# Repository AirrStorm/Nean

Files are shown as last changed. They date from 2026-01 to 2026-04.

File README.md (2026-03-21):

# Nean
A custom made 3d printed tendon driven robotic hand made to learn more about mechanical designs and a bit of biology. It is loosely based on how the human hand actually works. It uses strings to pull the fingers open and close similar to real muscles in the palm. It uses a python script to read finger positions and controls the movement of the hand.

---

## 🧰 Parts Needed

- Arduino Uno
- 2 18650 li-ion batteries
- Switch
- 16-Channel 12-bit PWM/Servo Driver - PCA9685
- 5 MG90s servos
- Elastic Cord
- Fishing Line
- Buck Converter LM2596S
  
---

## Wiring
Here is a preview of the wiring:

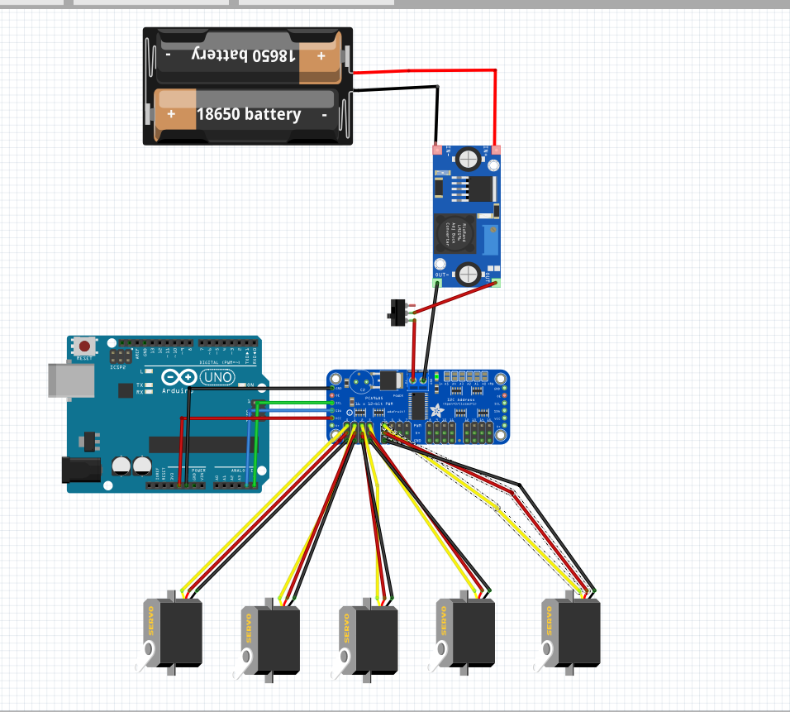
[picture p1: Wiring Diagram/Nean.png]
Wiring Preview


You can find the wiring diagram here:
```
Nean/
├── Wiring Diagram/
   └── Nean.png
```

---

## 3d Models
You can find the STEP files here:

```
Nean/
└──  STEP files/
```
And the STL files here:

```
Nean/
└──  STL files/
```
When 3d printing the models, for the fingers, only 3d print the parts that have "phalanx" at the end, the ones with "Finger" at the end are the full models of the fingers if you want to make changes. And for the arm models, print everything except the "Arm.step" file, which is the full 3d model of the arm if you want to make changes.

Here is a preview of the 3d model:



--- 

## Firmware

You can find the firmware files at:
```
Nean/
└──  Code/
```
It consist of a python file that runs on yout computer and one you upload to the Arduino.
The control system is simple, the python file checks if you hand is open or closed an sends it to the Arduino via serial communication (I plan to change to wifi later)

---

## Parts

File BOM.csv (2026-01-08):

Electronics
Item No. | Quantitiy | Part Name | Source | Links | Price
1 | 1 | ESP 32 | AliExpress | https://www.aliexpress.com/item/1005006984793820.html | $4.56
2 | 1 | PCA9685 Servo Driver | AliExpress | https://www.aliexpress.com/item/1005009595510490.html | $5.71
3 | 1 | DC-DC Buck Converter | AliExpress | https://www.aliexpress.com/item/1005007514313234.html | $3
4 | 1 | TP4056 Charger Module | AliExpress | https://www.aliexpress.com/item/1005009438302489.html | $4
5 | 1 | Slide Switch | Nauvitel Electronics (Local Vendor) | https://nauvitel.com/product/mini-slide-switch/ | $0.50
6 | 2 | 18650 Li-ion Battery | Oku Electronics (Local Vendor) | https://www.okuelectronics.com/store/prototyping/18650-2000mah-round-end-rechargeable-lithium-battery-3-7v-2pcs/ | $10
Actuation
Item No. | Quantity | Part Name | Source | Links | Price
7 | 5 | MG996R Servo | Alixpress | https://www.aliexpress.com/item/1005008658530145.html | $25.31
8 | 1 | Elastic Cord (10 meters) | Alixpress | https://www.aliexpress.com/item/1005008804282381.html | $5.19
9 | 1 | Fishing Line (1.0-0.165mm-5.39LB) | Alixpress | https://www.aliexpress.com/item/1005005245756703.html | $2.74
Wiring
Item No. | Quantity | Part Name | Source | Links | Price
10 | 1 | 2 x 18650 Battery Holder | Nauvitel Electronics (Local Vendor) | https://nauvitel.com/product/18650-3-7v-battery-holder-single/ | $1.50
11 | 5 | Servo Extension Cables (300mm) | AliExpress | https://www.aliexpress.com/item/32921410942.html | $2.26
12 | - | Jumper Wires
Tools and Miscellaneous
Item No. | Quantity | Part Name | Source | Links | Price
13 | 50 | 5 x 2 neodymium magnets | AliExpress | https://www.aliexpress.com/item/1005009966591112.html | $5.72
14 | 1 | Soldering Iron
15 | 1 | Hot glue gun
 | TOTAL | $70.68

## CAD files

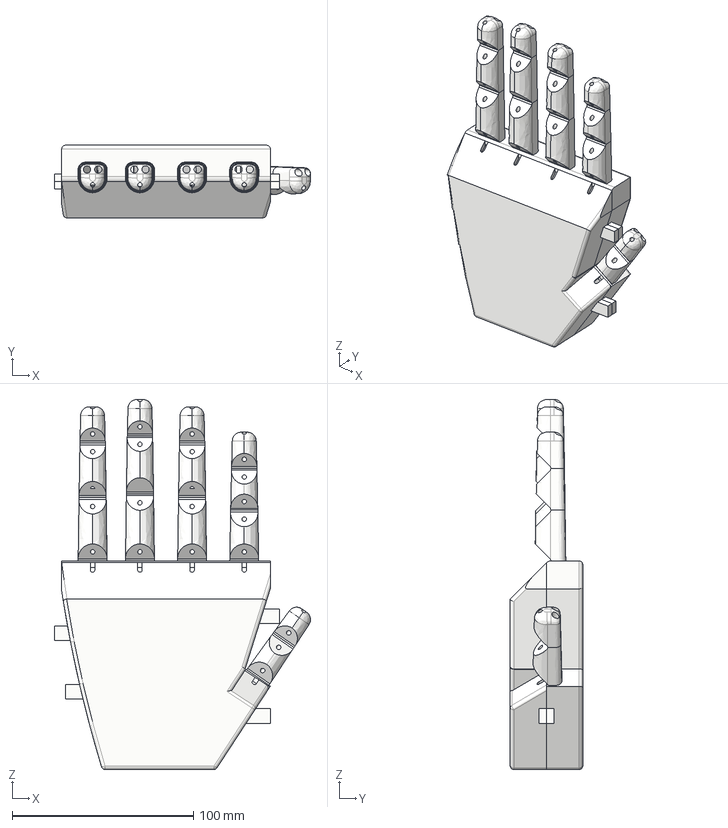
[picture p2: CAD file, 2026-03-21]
STEP files/Hand.step
141.2 x 40.0 x 204.0 mm
Index distal
Index middle
Index proximal
Middle distal
Middle middle
Middle proximal
Ring distal
Ring Middle
Ring proximal
Pinky middle
Pinky proximal
Pinky distal
Thumb distal
Thumb proximal

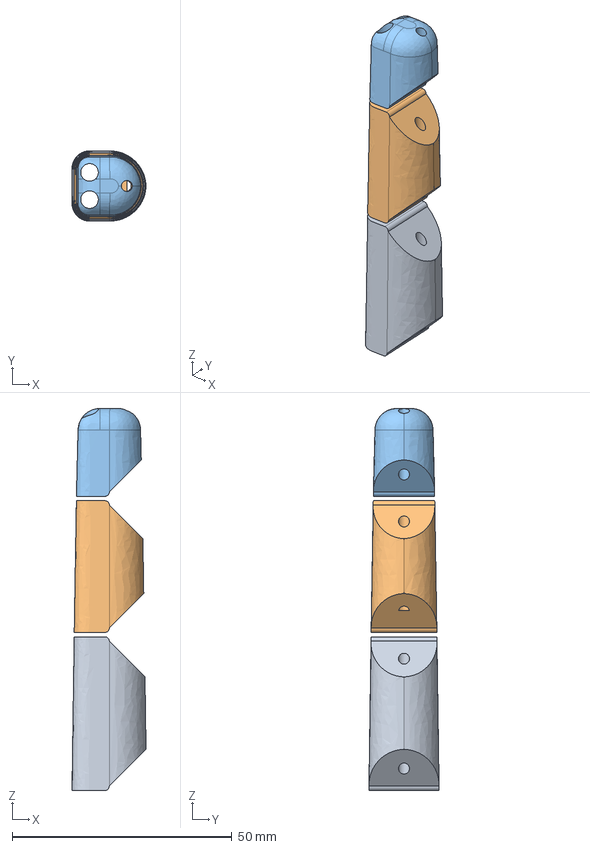
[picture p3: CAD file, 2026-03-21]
STEP files/Parts/Index Finger.step
16.9 x 16.0 x 87.0 mm
Proximal phalanx
Middle phalanx
Distal phalanx

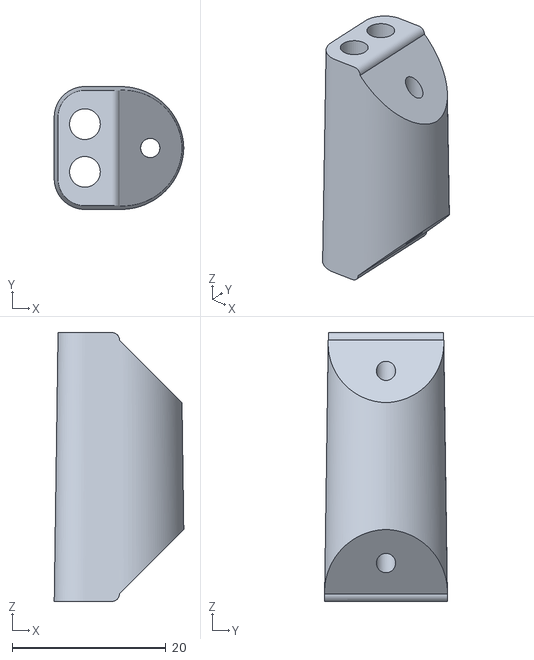
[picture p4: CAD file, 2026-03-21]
STL files/Index proximal phalanx.stl
16.9 x 16.0 x 35.0

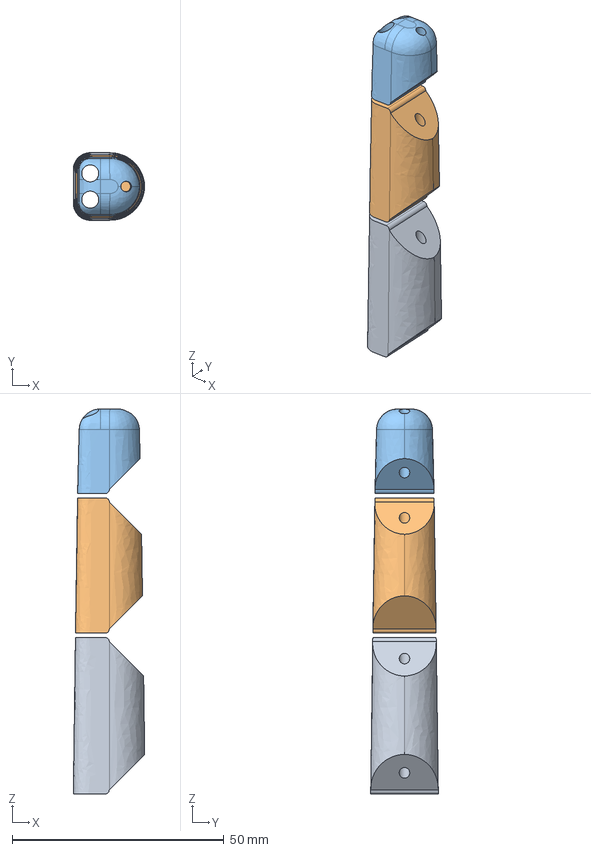
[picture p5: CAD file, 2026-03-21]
STEP files/Parts/Middle Finger.step
16.9 x 16.0 x 91.0 mm
Proximal phalanx
Middle phalanx
Distal phalanx

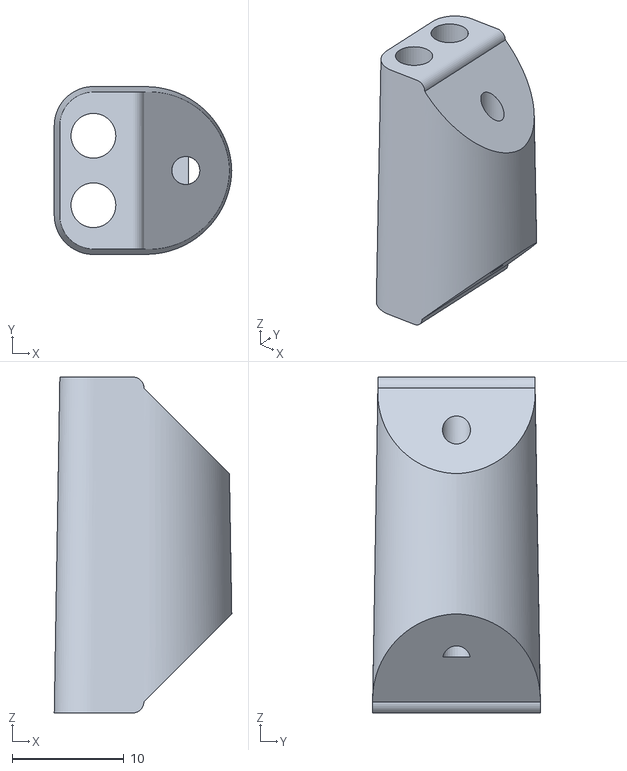
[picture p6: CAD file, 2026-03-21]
STL files/Index middle phalanx.stl
15.9 x 15.0 x 30.0

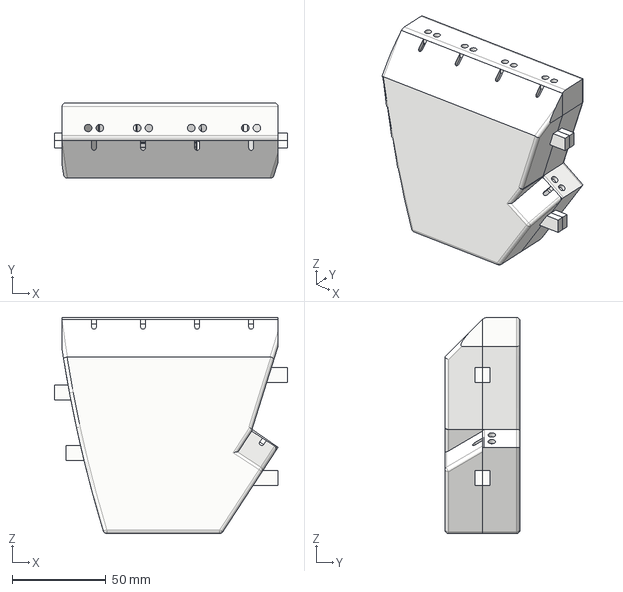
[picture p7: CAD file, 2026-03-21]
STEP files/Parts/Palm.step
124.0 x 40.0 x 115.0 mm

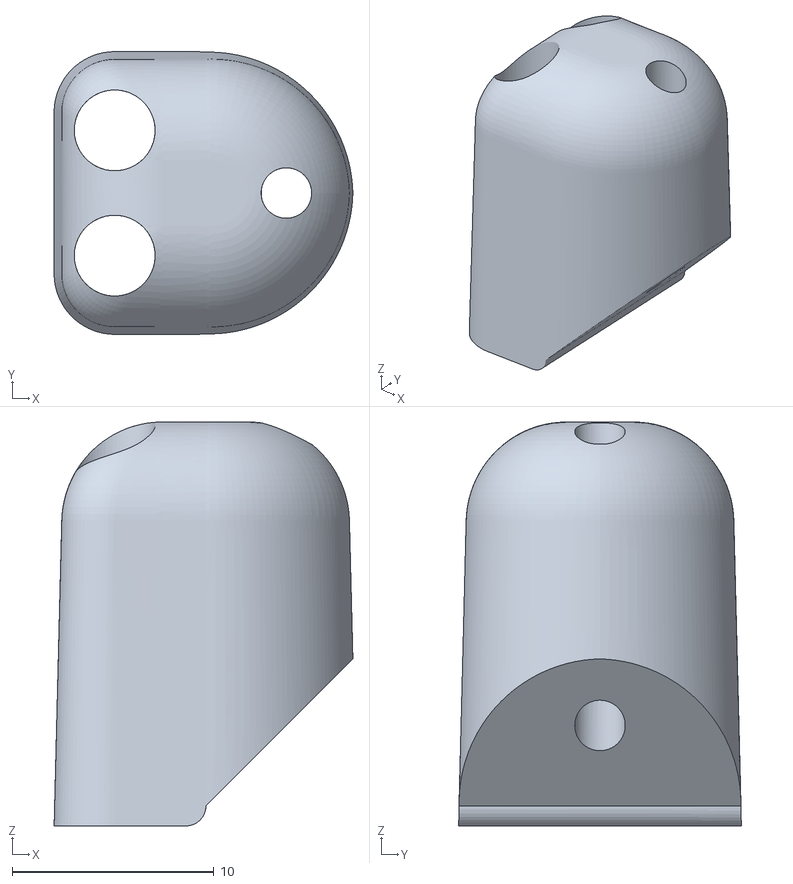
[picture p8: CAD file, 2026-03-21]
STL files/Index distal phalanx.stl
14.8 x 14.0 x 20.0

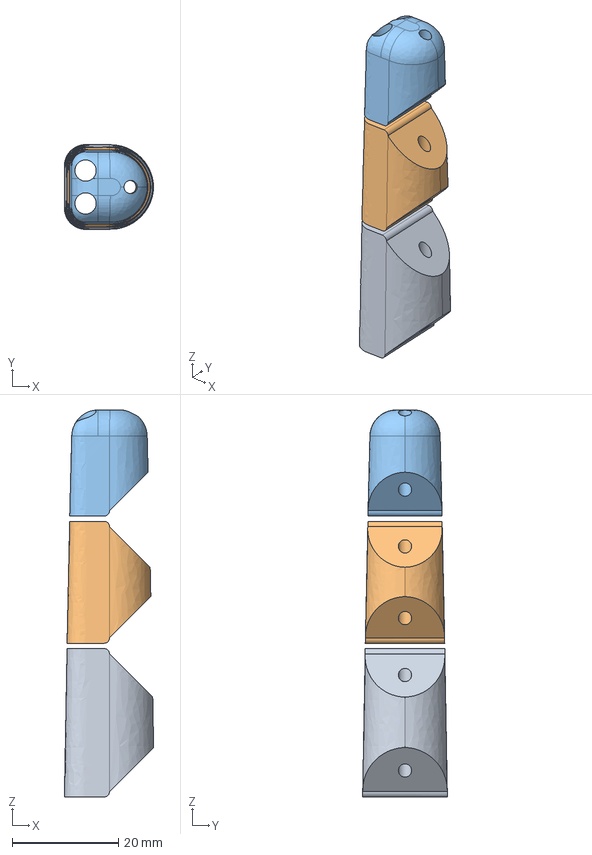
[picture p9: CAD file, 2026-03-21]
STEP files/Parts/Pinky Finger.step
16.8 x 16.0 x 73.0 mm
Proximal phalanx
Middle phalanx
Distal phalanx

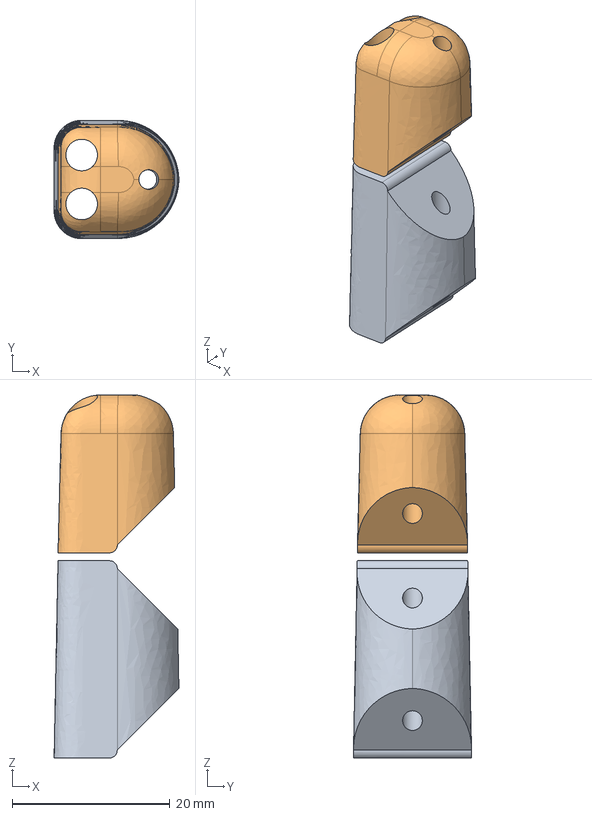
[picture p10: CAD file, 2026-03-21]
STEP files/Parts/Thumb.step
15.8 x 15.0 x 46.0 mm
Middle phalanx
Distal phalanx

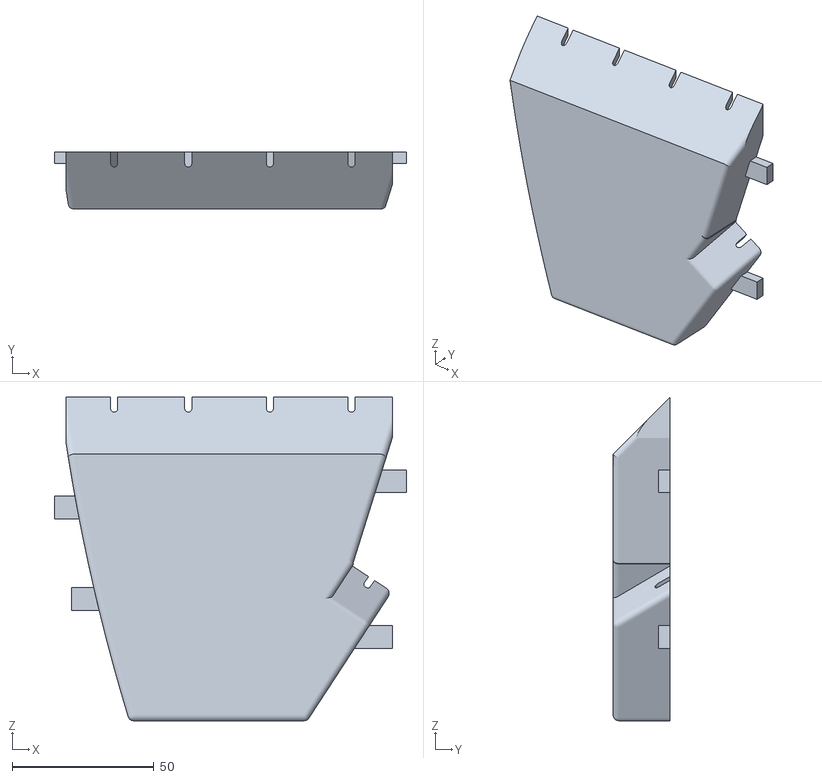
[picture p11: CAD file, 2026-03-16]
STL files/Palm 2.stl
124.0 x 20.0 x 114.0

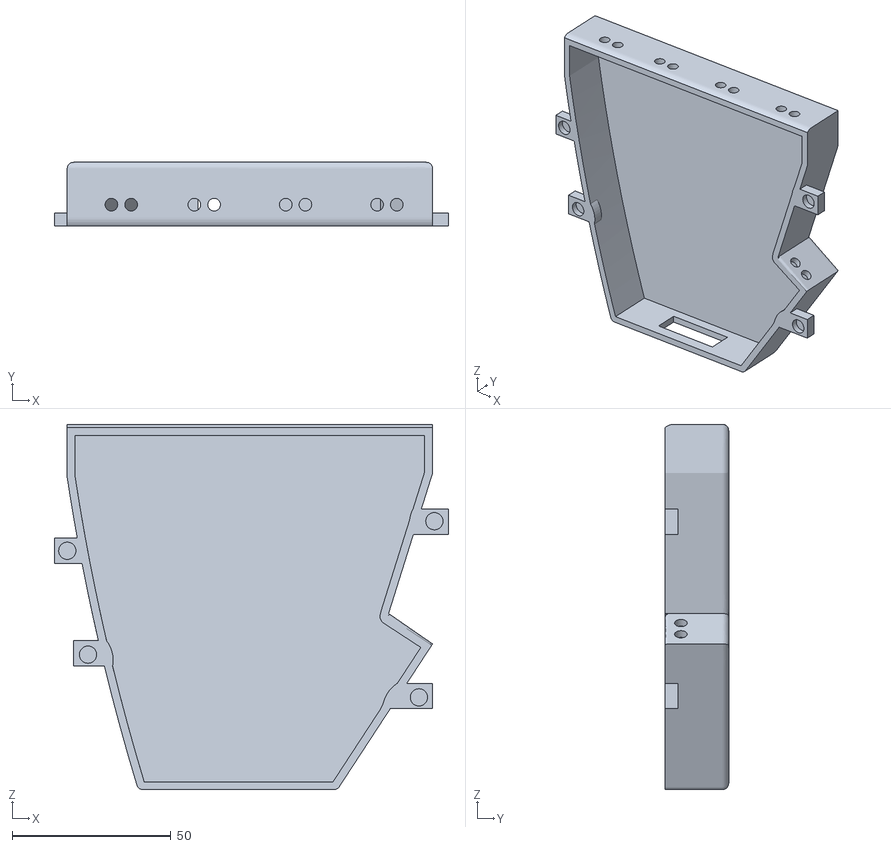
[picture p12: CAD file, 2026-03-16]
STL files/Palm 1.stl
124.0 x 20.0 x 115.0

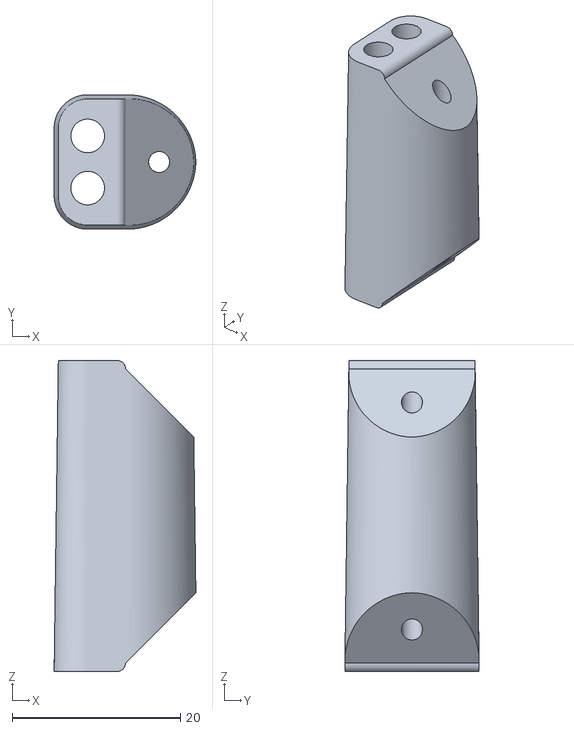
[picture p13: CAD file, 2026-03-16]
STL files/Middle proximal phalanx.stl
16.9 x 16.0 x 37.0

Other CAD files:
STL files/Ring middle phalanx.stl
STEP files/Parts/Ring Finger.step
STL files/Ring distal phalanx.stl
STL files/Pinky distal phalanx.stl
STL files/Thumb distal phalanx.stl
STL files/Ring proximal phalanx.stl
STL files/Middle distal phalanx.stl
STL files/Middle middle phalanx.stl
STL files/Pinky middle phalanx.stl
STL files/Pinky proximal phalanx.stl
STL files/Thumb proximal phalanx.stl

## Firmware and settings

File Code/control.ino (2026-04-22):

#include <Wire.h>
#include <Adafruit_PWMServoDriver.h>

Adafruit_PWMServoDriver pwm = Adafruit_PWMServoDriver();

#define SERVOMIN 110
#define SERVOMAX 640
#define SERVO_FREQ 50

// Channels
#define THUMB  0
#define INDEX  1
#define MIDDLE 2
#define RING   3
#define PINKY  4

uint16_t angleToPulse(int angle) {
  return map(angle, 0, 180, SERVOMIN, SERVOMAX);
}

void setup() {
  Serial.begin(115200);
  pwm.begin();
  pwm.setPWMFreq(SERVO_FREQ);
  delay(10);

  // Start all fingers open
  pwm.setPWM(THUMB,  0, angleToPulse(0));
  pwm.setPWM(INDEX,  0, angleToPulse(0));
  pwm.setPWM(MIDDLE, 0, angleToPulse(0));
  pwm.setPWM(RING,   0, angleToPulse(130));
  pwm.setPWM(PINKY,  0, angleToPulse(130));
}

void loop() {
  if (Serial.available()) {

    String data = Serial.readStringUntil('\n');

    // -------------------
    // THUMB
    // -------------------
    if (data.indexOf("thumb:closed") >= 0) {
      pwm.setPWM(THUMB, 0, angleToPulse(130));
    }
    if (data.indexOf("thumb:open") >= 0) {
      pwm.setPWM(THUMB, 0, angleToPulse(0));
    }

    // -------------------
    // INDEX (uses swapped logic)
    // -------------------
    if (data.indexOf("index:closed") >= 0) {
      pwm.setPWM(INDEX, 0, angleToPulse(130));
    }
    if (data.indexOf("index:open") >= 0) {
      pwm.setPWM(INDEX, 0, angleToPulse(0));
    }

    // -------------------
    // MIDDLE (same as index)
    // -------------------
    if (data.indexOf("middle:closed") >= 0) {
      pwm.setPWM(MIDDLE, 0, angleToPulse(130));
    }
    if (data.indexOf("middle:open") >= 0) {
      pwm.setPWM(MIDDLE, 0, angleToPulse(0));
    }

    // -------------------
    // RING (opposite logic)
    // -------------------
    if (data.indexOf("ring:closed") >= 0) {
      pwm.setPWM(RING, 0, angleToPulse(0));
    }
    if (data.indexOf("ring:open") >= 0) {
      pwm.setPWM(RING, 0, angleToPulse(130));
    }

    // -------------------
    // PINKY (same as ring)
    // -------------------
    if (data.indexOf("pinky:closed") >= 0) {
      pwm.setPWM(PINKY, 0, angleToPulse(0));
    }
    if (data.indexOf("pinky:open") >= 0) {
      pwm.setPWM(PINKY, 0, angleToPulse(130));
    }
  }
}

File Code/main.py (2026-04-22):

import serial
import time

#Uncomment if on Wayland
# import os
# os.environ["QT_QPA_PLATFORM"] = "xcb"


## Import stuff
import cv2 as cv
import mediapipe as mp
from mediapipe.tasks import python
from mediapipe.tasks.python import vision
from math import sqrt


ser = serial.Serial('/dev/ttyACM0', 115200)

cam = cv.VideoCapture(0)
BaseOptions = mp.tasks.BaseOptions
HandLandmarker = mp.tasks.vision.HandLandmarker
HandLandmarkerOptions = mp.tasks.vision.HandLandmarkerOptions
HandResult = mp.tasks.vision.HandLandmarkerResult
VisionRunningMode = mp.tasks.vision.RunningMode


latest_result = None
latest_hand = None
latest_frame = None


def print_result(result: HandResult, output_image: mp.Image, timestamp_ms: int): # type: ignore
    global latest_result
    latest_result = result

def draw_landmarks(frame, result):
    if result is None:
        return frame

    h, w, _ = frame.shape

    for hand in result.hand_landmarks:

        points = []

        for lm in hand:
            x = int(lm.x * w)
            y = int(lm.y * h)

            points.append((x, y))
            cv.circle(frame, (x, y), 5, (255, 255, 0), -1)

        connections = [
            (0,1),(1,2),(2,3),(3,4),
            (0,5),(5,6),(6,7),(7,8),
            (5,9),(9,10),(10,11),(11,12),
            (9,13),(13,14),(14,15),(15,16),
            (13,17),(17,18),(18,19),(19,20),
            (0,17)
        ]

        for c in connections:
            cv.line(frame, points[c[0]], points[c[1]], (0, 165, 255), 3)

    return frame

options = HandLandmarkerOptions(
    base_options=BaseOptions(model_asset_path='hand_landmarker.task'),
    running_mode=VisionRunningMode.LIVE_STREAM,
    result_callback=print_result)

def get_pixel(part_name):
    global latest_hand, latest_frame

    if latest_hand is None or latest_frame is None:
        return None

    landmarks = {
        "wrist": 0,

        "thumb_mcp": 2,
        "thumb_ip": 3,
        "thumb_tip": 4,

        "index_mcp": 5,
        "index_pip": 6,
        "index_dip": 7,
        "index_tip": 8,

        "middle_mcp": 9,
        "middle_pip": 10,
        "middle_dip": 11,
        "middle_tip": 12,

        "ring_mcp": 13,
        "ring_pip": 14,
        "ring_dip": 15,
        "ring_tip": 16,

        "pinky_mcp": 17,
        "pinky_pip": 18,
        "pinky_dip": 19,
        "pinky_tip": 20,
    }

    idx = landmarks[part_name]
    lm = latest_hand[idx]

    h, w, _ = latest_frame.shape

    x = int(lm.x * w)
    y = int(lm.y * h)

    magnitude = sqrt(x**2 + y**2)

    return magnitude

timestamp = 0

with HandLandmarker.create_from_options(options) as landmarker:


    while True:

        ret, frame = cam.read()

        if not ret:
            print("Camera not working")
            break


        mp_image = mp.Image(
            image_format=mp.ImageFormat.SRGB,
            data=frame
        )

        frame_rgb = cv.cvtColor(frame, cv.COLOR_BGR2RGB)
        
        mp_image = mp.Image(image_format=mp.ImageFormat.SRGB, data=frame_rgb)
        timestamp += 1

        land = landmarker.detect_async(mp_image,timestamp)

            
        latest_frame = frame

        if latest_result and latest_result.hand_landmarks:
            latest_hand = latest_result.hand_landmarks[0]
        

        finger_map = {
            "thumb": ("thumb_tip", "thumb_ip"),
            "index": ("index_tip", "index_pip"),
            "middle": ("middle_tip", "middle_pip"),
            "ring": ("ring_tip", "ring_pip"),
            "pinky": ("pinky_tip", "pinky_pip"),
        }

        finger_states = {}

        for finger, (tip_name, pip_name) in finger_map.items():

            tip = get_pixel(tip_name)
            pip = get_pixel(pip_name)

            if tip is None or pip is None:
                continue

            # Thumb uses X axis
            if finger == "thumb":
                if tip > pip:  # Adjust direction if needed
                    finger_states[finger] = "open"
                else:
                    finger_states[finger] = "closed"

            # Other fingers use Y axis
            else:
                if tip < pip:
                    finger_states[finger] = "open"
                else:
                    finger_states[finger] = "closed"

        print(finger_states)
        # Convert to Arduino string
        # Default state if no hand detected
        default_state = 'open'  
        arduino_fingers = ['thumb','index', 'middle', 'ring', 'pinky']

        # Fill in missing fingers with default
        for f in arduino_fingers:
            if f not in finger_states:
                finger_states[f] = default_state

        arduino_string = ",".join(f"{f}:{finger_states[f]}" for f in arduino_fingers) + "\n"
        print(arduino_string)

        ser.write(arduino_string.encode())

        annotated = draw_landmarks(frame, latest_result)

        cv.imshow("deez", annotated)

        key = cv.waitKey(1)

        if key == ord('q'):
            break

cam.release()
cv.destroyAllWindows()

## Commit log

2025-12-08 Added 3d models
    [Index Finger.f3d, Index distal phalanx.stl, Index middle phalanx.stl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]
2025-12-08 Added Wiring Diagram
2025-12-08 Added the case for everything
    [Base.stl, Forearm 1.stl, Forearm 2.stl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]
2025-12-08 Added the fusion 360 file for the Arm
2025-12-08 Enhance README with parts and wiring details
    Added parts list and wiring information for the Nean robotic hand.
2025-12-08 Fix image path for wiring preview in README
2025-12-08 Updated README
    Added 3D models section with STL and Fusion 360 files information.
2025-12-09 Added mounting Holes for fingers
    [Palm.stl]
2025-12-10 Added magnets holes
2025-12-11 Fixed a problem with the middle distal phalanx
    [Middle distal phalanx.stl]
2025-12-25 Added BOM
    [BOM.csv]
2025-12-31 Added New Palm design
    [Palm 1.stl, Palm 2.stl]
2026-01-04 Added Step files
    [Arm.step, Base.step, Forearm 1.step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]
2026-01-04 Added Palm step files
    [Palm 1.step, Palm 2.step]
2026-01-04 Revise 3D model file references in README
    Updated file references and printing instructions for 3D models.
2026-01-08 Updated BOM.csv
    [BOM.csv]
2026-01-29 Updated step files
    Added mounting holes for servos and added fillets and chamfers to other parts
    [Base.step, Forearm 1.step, Forearm 2.step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]
2026-01-29 Updated step files
    Added mounting holes for servos and fillets and chamfers for other parts
    [Arm.step, Base.step, Forearm 1.step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]
2026-02-11 Added mounting holes for electronics
    [Arm.step]
2026-03-16 Update servo and power supply components in README
2026-03-16 Added new updated STL files
    [Middle distal phalanx (redesigned).stl, Middle middle phalanx (redesigned).stl, Middle proximal phalanx (redesgined).stl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]
2026-03-16 Update STEP files reference to STL files
2026-03-21 Added STEP files for easier modification
    [Hand.step, Index Finger.step, Middle Finger.step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]
2026-03-21 Update README with 3D printing instructions
    Clarified instructions for 3D printing models and file locations.
2026-03-21 Added updated stl files
    [Index distal phalanx.stl, Index middle phalanx.stl, Index proximal phalanx.stl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]
2026-03-21 Fix typos and update device references in README
    Updated references from ESP32 to Arduino and corrected typos.
2026-04-22 Refactor finger channel definitions and logic
